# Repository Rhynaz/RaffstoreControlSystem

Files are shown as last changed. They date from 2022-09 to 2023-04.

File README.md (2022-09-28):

# Raffstore Control System (RCS)
> Web enabled relay board with hardware button support for easy smart home integration

## Features
Hardware:
- 9 - 30 VDC power supply
- ESP32-S3 Microcontroller
- 7 channels with two inputs and two outputs each
- inputs and outputs rated for 230 VAC / 325DC
- inputs and outputs galvanically isolated
- outputs fused
- outputs mutually exclusive (both off, only one on)
- 10-100 Mbps Ethernet connection
- 2.4 GHz 802.11 b/g/n Wi-Fi connection
- UART connection
- UART and JTAG over USB-B

Software:
- simple HTTP API with per and all channel controls
- Wi-Fi fallback if no Ethernet connection
- web interface based on simple HTTP API (See [Web Interface and HTTP API](#web-interface-and-http-api))
- time based automatic output disabling (See [Stop Timeout](#stop-timeout))
- [hardware button pattern recognition](#hardware-buttons)
- simple profile based [configuration](#project-configuration)
- [OTA update support](#firmware-upgrade)

## Repository Layout
| Path | Description |
| :---: | :---: |
| `hardware/` | KiCad 6 schematics and pcb layout |
| `software/` | ESP-IDF component directory |
| `software/config/` | [firmware config system](#project-configuration) |
| `software/controller/` | relay and switch controller handling hardware I/O |
| `software/http/` | web server serving the web interface and HTTP API |
| `software/main/` | firmware entrypoint |
|  `software/network/` | background network service |
| `software/update/` | [OTA update](#firmware-upgrade) service |
| `partitions.csv` | partition table for ESP32-S3 with 8 MB flash |
|  `sdkconfig.defaults`  | ESP-IDF project config for generating the full config |
| `thunder.json` | Thunder Client config for [OTA update](#firmware-upgrade) |

## Usage

### Web Interface and HTTP API
The web interface and HTTP API is served on port 80. Every channel can be opened (1st output on), closed (2nd output on) and stopped (both outputs off).
This can be done though the API by sending a `POST` request to `/actions/<action>/<channel_num>` where `<action>` is either `open`, `close` or `stop`, and `channel_num` is between including 0 and excluding the configured number of channels. Additionally channels can be controlled all at once by omiting the `/<channel_num>`. This is also possible in the web interface.

### Stop Timeout
Each channel has a configurable stop timeout, which is the longest time a channel has one of its output on. The timeout starts / resets with each open or close request.
After reaching the timeout the channel is stopped. This ensures minimal idle power usage and stress on the motor.

### Hardware Buttons
Two buttons are supported per channel and are used one for opening and the other for closing.
Each button supports basic pattern matching to accommodate three different control modes:
1. Press and hold to move the channel until the button is released.
2. Single click the button move the channel until the button is pressed again or the stop timeout is reached.
3. Double click the button to move all channel at the same time until the button is pressed again or the stop timeout is reached.

### Project Configuration
The configuration system utilizes `#define` statements from the currently active profile. A profile consists of a single header file in `software/config/include/config/profiles/` and an entry in `config/Kconfig`. It is recommended to create a copy of the default profile and start tweaking from there. The active config profile can be selected with ESP-IDF menuconfig under `Component Config > Raffstore Control System`.

### Firmware Upgrade
The firmware can be upgraded either over UART, USB or over-the-air (OTA) with HTTP over Ethernet or Wi-Fi. For the wired approaches use the ESP-IDF flashing tool and flash `build/RaffstoreControlSystem.elf`. The OTA update requires the use of a HTTP client (e.g. Thunder Client). To start the update, send a POST request to `/flash` with the firmware image as the body. Do not use multipart form data file upload, instead just put the raw binary data in the body. Use `build/RaffstoreControlSystem.bin` for OTA updates. The server will not send a response, it will apply the update and reboot. If the image gets corrupted during upload or flashing, the update is invalidated and the previous firmware will be used.

## License
RaffstoreControlSystem - Web enabled relay board with hardware button support for easy smart home integration<br>
Copyright (C) 2022 The Rhynaz

This program is free software: you can redistribute it and/or modify
it under the terms of the GNU General Public License as published by
the Free Software Foundation, either version 3 of the License, or
any later version.

This program is distributed in the hope that it will be useful,
but WITHOUT ANY WARRANTY; without even the implied warranty of
MERCHANTABILITY or FITNESS FOR A PARTICULAR PURPOSE. See the
GNU General Public License for more details.

You should have received a copy of the GNU General Public License
along with this program. If not, see <https://www.gnu.org/licenses/>.

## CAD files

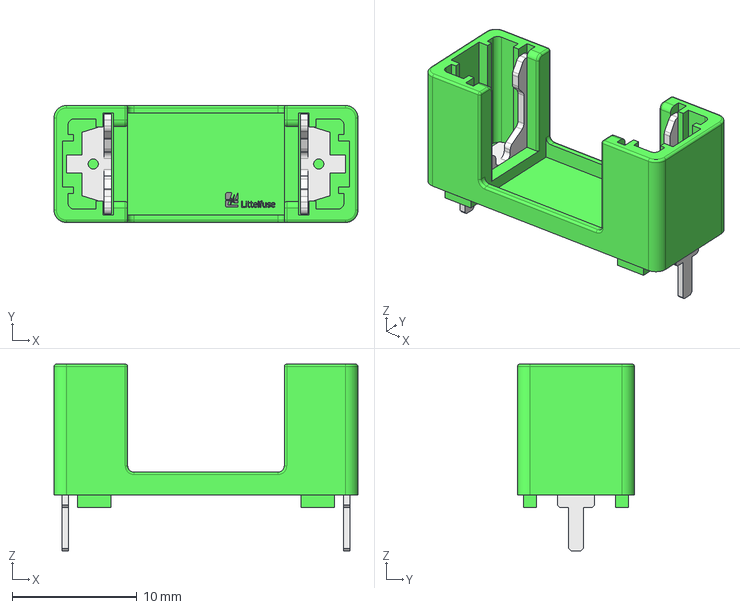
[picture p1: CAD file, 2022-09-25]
hardware/0PTF0078P/0PTF0078P.step
24.4 x 9.40 x 15.0 mm

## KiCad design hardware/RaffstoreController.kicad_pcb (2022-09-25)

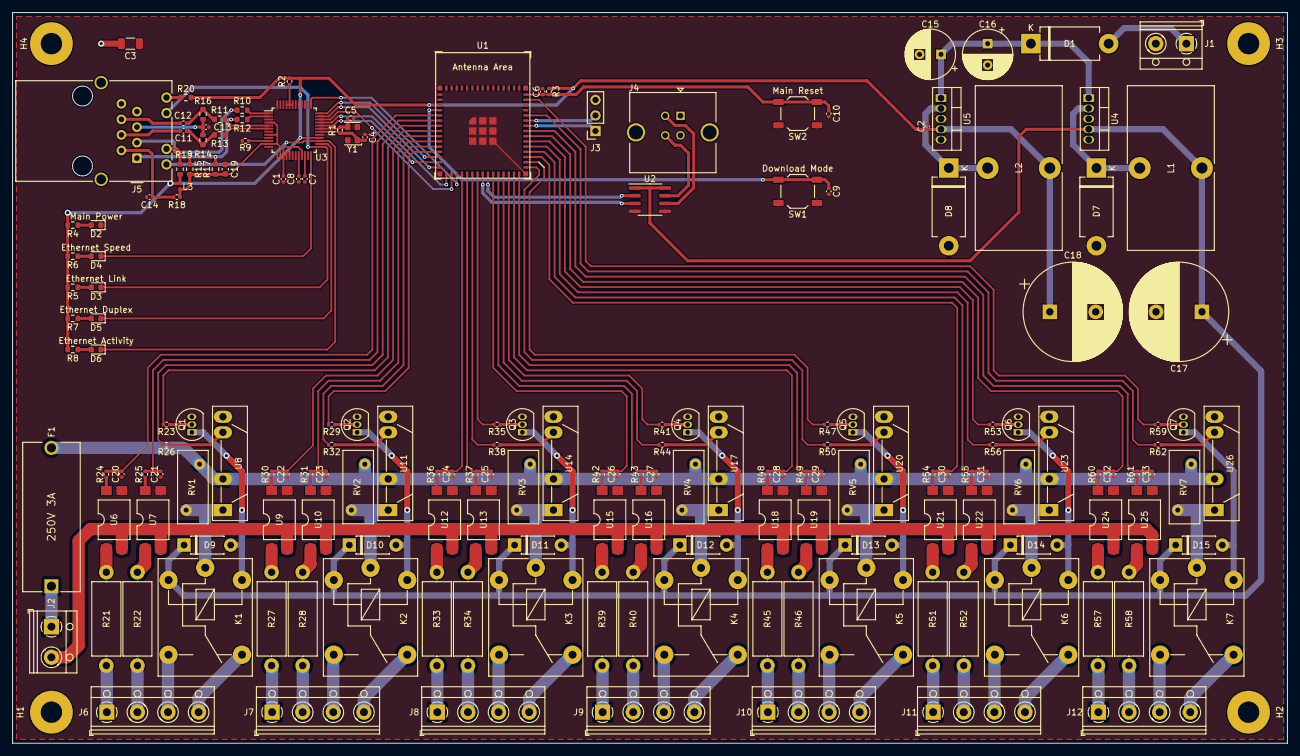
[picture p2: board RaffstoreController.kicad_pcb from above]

Board: 2 copper layers, 208.3 x 119.4 mm, 180 parts (0 on the bottom side), 167 nets.

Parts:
C1, C2, C9, C10: 100nF; C_0402_1005Metric
C3: 1nF; C_1206_3216Metric
C4, C5: 18pF; C_0402_1005Metric
C6, C20, C21, C22, C23, C24, C25, C26, C27, C28, C29, C30, C31, C32, C33: 1µF; C_0402_1005Metric
C7, C13: 10nF; C_0402_1005Metric
C8: 4.7µF; C_0402_1005Metric
C11, C12: 6.8nF; C_0402_1005Metric
C14: 22nF; C_0402_1005Metric
C15, C16: 100µF; CP_Radial_D8.0mm_P3.50mm
C17, C18: 1000µF; CP_Radial_D16.0mm_P7.50mm
C19: 10µF; C_0603_1608Metric
D1, D7, D8: 1N5822; D_DO-201AD_P12.70mm_Horizontal
D2: Main Power; LED_0603_1608Metric
D3: Ethernet Link; LED_0603_1608Metric
D4: Ethernet Speed; LED_0603_1608Metric
D5: Ethernet Duplex; LED_0603_1608Metric
D6: Ethernet Activity; LED_0603_1608Metric
D9, D10, D11, D12, D13, D14, D15: 1N4001; D_DO-41_SOD81_P7.62mm_Horizontal
F1: 250V 3A; 0PTF0078P
H1, H2, H3, H4: Mounting Hole; MountingHole_3.5mm_Pad
J1: DC 7-30V; TerminalBlock_RND_205-00012_1x02_P5.00mm_Horizontal
J2: AC 230V; TerminalBlock_RND_205-00012_1x02_P5.00mm_Horizontal
J3: Serial; PinSocket_1x03_P2.54mm_Vertical
J4: USB; USB_B_TE_5787834_Vertical
J5: 7499010121A; RJ45_Wuerth_7499010121A_Horizontal
J6, J7, J8, J9, J10, J11, J12: Raffstore; TerminalBlock_RND_205-00014_1x04_P5.00mm_Horizontal
K1, K2, K3, K4, K5, K6, K7: FINDER-36.11.9.005; Relay_SPDT_Finder_36.11
L1, L2: 100µH; L_Toroid_Vertical_L26.7mm_W14.0mm_P10.16mm_Pulse_D
L3: Ferrite Bead; L_0402_1005Metric
Q1, Q2, Q3, Q4, Q5, Q6, Q7: BC337; TO-92_Inline
R1: 1MΩ; R_0402_1005Metric
R2, R3, R23, R29, R35, R41, R47, R53, R59: 10kΩ; R_0402_1005Metric
R4, R5, R8, R19, R20: 62Ω; R_0603_1608Metric
R6, R7: 20Ω; R_0603_1608Metric
R9: 12.4kΩ; R_0402_1005Metric
R10, R11, R12, R13: 33Ω; R_0603_1608Metric
R14, R16: 82Ω; R_0603_1608Metric
R15, R17: 49.9Ω; R_0603_1608Metric
R18: 10Ω; R_0402_1005Metric
R21, R22, R27, R28, R33, R34, R39, R40, R45, R46, R51, R52, R57, R58: 430kΩ; R_Axial_DIN0414_L11.9mm_D4.5mm_P15.24mm_Horizontal
R24, R25, R30, R31, R36, R37, R42, R43, R48, R49, R54, R55, R60, R61: 1kΩ; R_0402_1005Metric
R26, R32, R38, R44, R50, R56, R62: 100Ω; R_0402_1005Metric
RV1, RV2, RV3, RV4, RV5, RV6, RV7: S10K275; RV_Disc_D12mm_W5mm_P7.5mm
SW1: Download Mode; SW_SPST_TL3342
SW2: Main Reset; SW_SPST_TL3342
U1: ESP32-S3-MINI-1
U2: USB6B1; SOIC-8_3.9x4.9mm_P1.27mm
U3: W5500; LQFP-48_7x7mm_P0.5mm
U4: LM2576T-5; TO-220-5_Vertical
U5: LM2576T-3.3; TO-220-5_Vertical
U6, U7, U9, U10, U12, U13, U15, U16, U18, U19, U21, U22, U24, U25: SFH6286-3T; SMDIP-4_W9.53mm_Clearance8mm
U8, U11, U14, U17, U20, U23, U26: S202S02; SIP4_Sharp-SSR_P7.62mm_Straight
Y1: 25MHz; Oscillator_SMD_EuroQuartz_XO32-4Pin_3.2x2.5mm

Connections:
+3.3VA: C1.2, C19.1, L3.2, R15.1, R17.1, R18.1, U3.4 (AVDD), U3.8 (AVDD), U3.11 (AVDD), U3.15 (AVDD), U3.17 (AVDD), U3.21 (AVDD)
+3V3: C2.2, C18.1, L2.2, L3.1, R2.1, R3.1, R4.2, R5.2, R6.2, R7.2, R8.2, R19.1, R20.2, U1.3 (3V3), U3.28 (VDD), U5.4 (FB)
+5V: C17.1, D9.1 (K), D10.1 (K), D11.1 (K), D12.1 (K), D13.1 (K), D14.1 (K), D15.1 (K), K1.A1, K2.A1, K3.A1, K4.A1, K5.A1, K6.A1, K7.A1, L1.2, U2.1 (VBUS), U2.8 (VBUS), U4.4 (FB)
/CLK: U1.16 (IO12/SPI_CLK), U3.33 (SCLK)
/D+: U1.24 (IO20/USB_D+), U2.2 (I/O1)
/D-: U1.23 (IO19/USB_D-), U2.3 (I/O2)
/IO1: C20.1, R24.2, U1.5 (IO01)
/IO2: C21.1, R25.2, U1.6 (IO02)
/IO3: R26.2, U1.7 (IO03)
/IO4: R23.2, U1.8 (IO04)
/IO5: C22.1, R30.2, U1.9 (IO05)
/IO6: C23.1, R31.2, U1.10 (IO06)
/IO7: R32.2, U1.11 (IO07)
/IO8: R29.2, U1.12 (IO08)
/IO15: C24.1, R36.2, U1.19 (IO15)
/IO16: C25.1, R37.2, U1.20 (IO16)
/IO17: R38.2, U1.21 (IO17)
/IO18: R35.2, U1.22 (IO18)
/IO21: C26.1, R42.2, U1.25 (IO21)
/IO26: C27.1, R43.2, U1.26 (IO26)
/IO33: R41.2, U1.28 (IO33)
/IO34: C28.1, R48.2, U1.29 (IO34)
/IO35: R50.2, U1.31 (IO35)
/IO36: R47.2, U1.32 (IO36)
/IO37: C30.1, R54.2, U1.33 (IO37)
/IO38: C31.1, R55.2, U1.34 (IO38)
/IO39: R56.2, U1.35 (IO39)
/IO40: R53.2, U1.36 (IO40)
/IO41: C32.1, R60.2, U1.37 (IO41)
/IO42: C33.1, R61.2, U1.38 (IO42)
/IO45: R62.2, U1.41 (IO45)
/IO46: R59.2, U1.44 (IO46)
/IO47: R44.2, U1.27 (IO47)
/IO48: C29.1, R49.2, U1.30 (IO48)
/MISO: U1.17 (IO13/SPI_MISO), U3.34 (MISO)
/MOSI: U1.15 (IO11/SPI_MOSI), U3.35 (MOSI)
/RD+: C11.2, J5.4 (RD+)
/RD-: C12.2, J5.6 (RD-)
/RX: J3.2, U1.40 (UART_RX/IO44)
/RX+: R13.1, U3.6 (RXP)
/RX-: R11.1, U3.5 (RXN)
/Raffstore Channel 0/MotorClose: J6.4, K1.12
/Raffstore Channel 0/MotorOpen: J6.3, K1.14
/Raffstore Channel 0/SwitchClose: J6.2, R22.1
/Raffstore Channel 0/SwitchOpen: J6.1, R21.1
/Raffstore Channel 1/MotorClose: J7.4, K2.12
/Raffstore Channel 1/MotorOpen: J7.3, K2.14
/Raffstore Channel 1/SwitchClose: J7.2, R28.1
/Raffstore Channel 1/SwitchOpen: J7.1, R27.1
/Raffstore Channel 2/MotorClose: J8.4, K3.12
/Raffstore Channel 2/MotorOpen: J8.3, K3.14
/Raffstore Channel 2/SwitchClose: J8.2, R34.1
/Raffstore Channel 2/SwitchOpen: J8.1, R33.1
/Raffstore Channel 3/MotorClose: J9.4, K4.12
/Raffstore Channel 3/MotorOpen: J9.3, K4.14
/Raffstore Channel 3/SwitchClose: J9.2, R40.1
/Raffstore Channel 3/SwitchOpen: J9.1, R39.1
/Raffstore Channel 4/MotorClose: J10.4, K5.12
/Raffstore Channel 4/MotorOpen: J10.3, K5.14
/Raffstore Channel 4/SwitchClose: J10.2, R46.1
/Raffstore Channel 4/SwitchOpen: J10.1, R45.1
/Raffstore Channel 5/MotorClose: J11.4, K6.12
/Raffstore Channel 5/MotorOpen: J11.3, K6.14
/Raffstore Channel 5/SwitchClose: J11.2, R52.1
/Raffstore Channel 5/SwitchOpen: J11.1, R51.1
/Raffstore Channel 6/MotorClose: J12.4, K7.12
/Raffstore Channel 6/MotorOpen: J12.3, K7.14
/Raffstore Channel 6/SwitchClose: J12.2, R58.1
/Raffstore Channel 6/SwitchOpen: J12.1, R57.1
/TD+: J5.1 (TD+), R12.2, R17.2
/TD-: J5.3 (TD-), R10.2, R15.2
/TX: J3.1, U1.39 (UART_TX/IO43)
/TX+: R12.1, U3.2 (TXP)
/TX-: R10.1, U3.1 (TXN)
/~CS: U1.14 (IO10/~SPI_CS), U3.32 (~SCS)
/~INT: U1.13 (IO09/~SPI_INT), U3.36 (~INT)
/~RST: U1.18 (IO14/~SPI_RST), U3.37 (~RST)
AC: F1.2, RV1.2, RV2.2, RV3.2, RV4.2, RV5.2, RV6.2, RV7.2, U8.2, U11.2, U14.2, U17.2, U20.2, U23.2, U26.2
ACT_LED: D6.1 (K), J5.9, U3.27 (ACTLED)
CPU_DLM: C9.2, SW1.2, U1.4 (IO00/DLM)
CPU_RST: C6.1, C10.2, R3.2, SW2.2, U1.45 (EN)
DUP_LED: D5.1 (K), U3.26 (DUPLED)
GND: C1.1, C2.1, C3.1, C4.2, C5.2, C6.2, C7.2, C8.2, C9.1, C10.1, C13.2, C14.2, C15.2, C16.2, C17.2, C18.2, C19.2, C20.2, C21.2, C22.2, C23.2, C24.2, C25.2, C26.2, C27.2, C28.2, C29.2, C30.2, C31.2, C32.2, C33.2, D2.1 (K), D7.2 (A), D8.2 (A), J1.2, J3.3, J4.4 (GND), Q1.3 (E), Q2.3 (E), Q3.3 (E), Q4.3 (E), Q5.3 (E), Q6.3 (E), Q7.3 (E), R9.1, SW1.1, SW2.1, U1.1 (GND), U1.2 (GND), U1.42 (GND), U1.43 (GND), U1.46 (GND), U2.4 (GND), U2.5 (GND), U3.3 (AGND), U3.9 (AGND), U3.14 (AGND), U3.16 (AGND), U3.19 (AGND), U3.29 (GND), U3.48 (AGND), U4.3 (GND), U4.5 (~ON/OFF), U5.3 (GND), U5.5 (~ON/OFF), U6.3, U7.3, U8.4, U9.3, U10.3, U11.4, U12.3, U13.3, U14.4, U15.3, U16.3, U17.4, U18.3, U19.3, U20.4, U21.3, U22.3, U23.4, U24.3, U25.3, U26.4, Y1.2, Y1.4
GNDPWR: J2.2, U6.2, U7.2, U9.2, U10.2, U12.2, U13.2, U15.2, U16.2, U18.2, U19.2, U21.2, U22.2, U24.2, U25.2
GNDREF: C3.2, H1.1, H2.1, H3.1, H4.1, J4.5 (Shield), J5.8, J5.SH
LNK_LED: D3.1 (K), J5.11, U3.25 (LINKLED)
unnamed: C4.1, R1.2, U3.30 (XI/CLKIN), Y1.1
unnamed: C5.1, R1.1, U3.31 (XO), Y1.3
unnamed: C7.1, U3.22 (1V2O)
unnamed: C8.1, U3.20 (TOCAP)
unnamed: C11.1, R13.2, R14.2
unnamed: C12.1, R11.2, R16.2
unnamed: C13.1, J5.5 (RCT), R14.1, R16.1
unnamed: C14.1, J5.2 (TCT), R18.2
unnamed: D1.2 (A), J1.1
unnamed: D2.2 (A), R4.1
unnamed: D3.2 (A), R5.1
unnamed: D4.2 (A), R6.1
unnamed: D5.2 (A), R7.1
unnamed: D6.2 (A), R8.1
unnamed: D7.1 (K), L1.1, U4.2 (OUT)
unnamed: D8.1 (K), L2.1, U5.2 (OUT)
unnamed: D9.2 (A), K1.A2, Q1.1 (C)
unnamed: D10.2 (A), K2.A2, Q2.1 (C)
unnamed: D11.2 (A), K3.A2, Q3.1 (C)
unnamed: D12.2 (A), K4.A2, Q4.1 (C)
unnamed: D13.2 (A), K5.A2, Q5.1 (C)
unnamed: D14.2 (A), K6.A2, Q6.1 (C)
unnamed: D15.2 (A), K7.A2, Q7.1 (C)
unnamed: F1.1, J2.1
unnamed: J4.2 (D-), U2.6 (I/O2)
unnamed: J4.3 (D+), U2.7 (I/O1)
unnamed: J5.10, R19.2
unnamed: J5.12, R20.1
unnamed: K1.11, RV1.1, U8.1
unnamed: K2.11, RV2.1, U11.1
unnamed: K3.11, RV3.1, U14.1
unnamed: K4.11, RV4.1, U17.1
unnamed: K5.11, RV5.1, U20.1
unnamed: K6.11, RV6.1, U23.1
unnamed: K7.11, RV7.1, U26.1
unnamed: Q1.2 (B), R23.1
unnamed: Q2.2 (B), R29.1
unnamed: Q3.2 (B), R35.1
unnamed: Q4.2 (B), R41.1
unnamed: Q5.2 (B), R47.1
unnamed: Q6.2 (B), R53.1
unnamed: Q7.2 (B), R59.1
unnamed: R2.2, U3.43 (PMODE2), U3.44 (PMODE1), U3.45 (PMODE0)
unnamed: R9.2, U3.10 (EXRES1)
unnamed: R21.2, U6.1
unnamed: R22.2, U7.1
unnamed: R24.1, U6.4
unnamed: R25.1, U7.4
unnamed: R26.1, U8.3
unnamed: R27.2, U9.1
unnamed: R28.2, U10.1
unnamed: R30.1, U9.4
unnamed: R31.1, U10.4
unnamed: R32.1, U11.3
unnamed: R33.2, U12.1
unnamed: R34.2, U13.1
unnamed: R36.1, U12.4
unnamed: R37.1, U13.4
unnamed: R38.1, U14.3
unnamed: R39.2, U15.1
unnamed: R40.2, U16.1
unnamed: R42.1, U15.4
unnamed: R43.1, U16.4
unnamed: R44.1, U17.3
unnamed: R45.2, U18.1
unnamed: R46.2, U19.1
unnamed: R48.1, U18.4
unnamed: R49.1, U19.4
unnamed: R50.1, U20.3
unnamed: R51.2, U21.1
unnamed: R52.2, U22.1
unnamed: R54.1, U21.4
unnamed: R55.1, U22.4
unnamed: R56.1, U23.3
unnamed: R57.2, U24.1
unnamed: R58.2, U25.1
unnamed: R60.1, U24.4
unnamed: R61.1, U25.4
unnamed: R62.1, U26.3
SPD_LED: D4.1 (K), U3.24 (SPDLED)
VCC: C15.1, C16.1, D1.1 (K), U4.1 (VIN), U5.1 (VIN)

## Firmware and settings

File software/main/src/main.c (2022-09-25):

#include "network.h"
#include "controller.h"
#include "http.h"
#include "update.h"

#include "esp_log.h"
#include "esp_event.h"
#include "driver/gpio.h"

static const char *const TAG = "Main       ";

void app_main()
{
    ESP_LOGI(TAG, "Raffstore Control System");
    ESP_LOGI(TAG, "Version " CONFIG_APP_PROJECT_VER);

    ESP_LOGI(TAG, "Register global ISR handler.");
    ESP_ERROR_CHECK(gpio_install_isr_service(0));

    ESP_LOGI(TAG, "Create default event loop.");
    ESP_ERROR_CHECK(esp_event_loop_create_default());

    ESP_LOGI(TAG, "Initialize network stack.");
    network_init();

    ESP_LOGI(TAG, "Initialize controller.");
    controller_init();

    ESP_LOGI(TAG, "Initialize HTTP server.");
    http_init();

    update_mark_valid();
}

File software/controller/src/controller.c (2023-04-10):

#include "controller.h"

#include "controller/channel.h"

#include "config.h"

#include "esp_log.h"
#include "esp_event.h"
#include "driver/gpio.h"

#define CONTROLLER_DEFINE_CHANNEL(num)                                         \
    [CONFIG_CONTROLLER_CHANNEL##num##_INDEX] = (channel_t)                     \
    {                                                                          \
        .index = CONFIG_CONTROLLER_CHANNEL##num##_INDEX,                       \
        .stop_timeout_sec = CONFIG_CONTROLLER_CHANNEL##num##_STOP_TIMEOUT_SEC, \
        .motor_enable = CONFIG_CONTROLLER_CHANNEL##num##_MOTOR_ENABLE,         \
        .motor_direction = CONFIG_CONTROLLER_CHANNEL##num##_MOTOR_DIRECTION,   \
        .motor_invert = CONFIG_CONTROLLER_CHANNEL##num##_MOTOR_INVERT,         \
        .switch_up = CONFIG_CONTROLLER_CHANNEL##num##_SWITCH_UP,               \
        .switch_down = CONFIG_CONTROLLER_CHANNEL##num##_SWITCH_DOWN,           \
        .switch_invert = CONFIG_CONTROLLER_CHANNEL##num##_SWITCH_INVERT,       \
    }

static const char *const TAG = "Controller ";

static channel_t channels[CONFIG_CONTROLLER_CHANNEL_NUM] = {
#ifdef CONFIG_CONTROLLER_CHANNEL0_ENABLE
    CONTROLLER_DEFINE_CHANNEL(0),
#endif
#ifdef CONFIG_CONTROLLER_CHANNEL1_ENABLE
    CONTROLLER_DEFINE_CHANNEL(1),
#endif
#ifdef CONFIG_CONTROLLER_CHANNEL2_ENABLE
    CONTROLLER_DEFINE_CHANNEL(2),
#endif
#ifdef CONFIG_CONTROLLER_CHANNEL3_ENABLE
    CONTROLLER_DEFINE_CHANNEL(3),
#endif
#ifdef CONFIG_CONTROLLER_CHANNEL4_ENABLE
    CONTROLLER_DEFINE_CHANNEL(4),
#endif
#ifdef CONFIG_CONTROLLER_CHANNEL5_ENABLE
    CONTROLLER_DEFINE_CHANNEL(5),
#endif
#ifdef CONFIG_CONTROLLER_CHANNEL6_ENABLE
    CONTROLLER_DEFINE_CHANNEL(6),
#endif
};

void controller_init()
{
    ESP_LOGI(TAG, "Configure GPIOs.");
    gpio_config_t switch_config = {
        .pin_bit_mask = 0,
        .mode = GPIO_MODE_INPUT,
        .pull_up_en = GPIO_PULLUP_ENABLE,
        .pull_down_en = GPIO_PULLDOWN_DISABLE,
        .intr_type = GPIO_INTR_DISABLE,
    };

    gpio_config_t motor_config = {
        .pin_bit_mask = 0,
        .mode = GPIO_MODE_INPUT_OUTPUT,
        .pull_up_en = GPIO_PULLUP_DISABLE,
        .pull_down_en = GPIO_PULLDOWN_DISABLE,
        .intr_type = GPIO_INTR_DISABLE,
    };

    for (uint8_t i = 0; i < CONFIG_CONTROLLER_CHANNEL_NUM; i++)
    {
        switch_config.pin_bit_mask |= (1ULL << channels[i].switch_up) | (1ULL << channels[i].switch_down);
        motor_config.pin_bit_mask |= (1ULL << channels[i].motor_enable) | (1ULL << channels[i].motor_direction);
    }

    ESP_ERROR_CHECK(gpio_config(&switch_config));
    ESP_ERROR_CHECK(gpio_config(&motor_config));

    ESP_LOGI(TAG, "Initialize channels.");
    for (uint8_t i = 0; i < CONFIG_CONTROLLER_CHANNEL_NUM; i++)
        channel_init(&channels[i]);
}

void controller_open(uint8_t channel_num, bool user_initiated)
{
    if (channel_num >= CONFIG_CONTROLLER_CHANNEL_NUM)
    {
        ESP_LOGE(TAG, "Tried opening channel %u of %u.", channel_num, CONFIG_CONTROLLER_CHANNEL_NUM);
        return;
    }

    esp_event_post_to(channels[channel_num].event_loop, CHANNEL_EVENT, CHANNEL_EVENT_OPEN, &user_initiated, sizeof(user_initiated), 0);
}

void controller_open_all(bool user_initiated)
{
    ESP_LOGI(TAG, "Open all channels.");

    for (uint8_t i = 0; i < CONFIG_CONTROLLER_CHANNEL_NUM; i++)
    {
        controller_open(i, user_initiated);
    }
}

void controller_close(uint8_t channel_num, bool user_initiated)
{
    if (channel_num >= CONFIG_CONTROLLER_CHANNEL_NUM)
    {
        ESP_LOGE(TAG, "Tried closing channel %u of %u.", channel_num, CONFIG_CONTROLLER_CHANNEL_NUM);
        return;
    }

    esp_event_post_to(channels[channel_num].event_loop, CHANNEL_EVENT, CHANNEL_EVENT_CLOSE, &user_initiated, sizeof(user_initiated), 0);
}

void controller_close_all(bool user_initiated)
{
    ESP_LOGI(TAG, "Close all channels.");

    for (uint8_t i = 0; i < CONFIG_CONTROLLER_CHANNEL_NUM; i++)
    {
        controller_close(i, user_initiated);
    }
}

void controller_stop(uint8_t channel_num, bool user_initiated)
{
    if (channel_num >= CONFIG_CONTROLLER_CHANNEL_NUM)
    {
        ESP_LOGE(TAG, "Tried stopping channel %u of %u.", channel_num, CONFIG_CONTROLLER_CHANNEL_NUM);
        return;
    }

    esp_event_post_to(channels[channel_num].event_loop, CHANNEL_EVENT, CHANNEL_EVENT_STOP, &user_initiated, sizeof(user_initiated), 0);
}

void controller_stop_all(bool user_initiated)
{
    ESP_LOGI(TAG, "Stop all channels.");

    for (uint8_t i = 0; i < CONFIG_CONTROLLER_CHANNEL_NUM; i++)
    {
        controller_stop(i, user_initiated);
    }
}

int8_t controller_query(uint8_t channel_num)
{
    if (channel_num >= CONFIG_CONTROLLER_CHANNEL_NUM)
    {
        ESP_LOGE(TAG, "Tried querying channel %u of %u.", channel_num, CONFIG_CONTROLLER_CHANNEL_NUM);
        return -1;
    }

    return channels[channel_num].last_user_event;
}

int8_t *controller_query_all()
{
    ESP_LOGI(TAG, "Query all channels.");

    static int8_t results[CONFIG_CONTROLLER_CHANNEL_NUM + 1];
    results[CONFIG_CONTROLLER_CHANNEL_NUM] = -1;

    for (uint8_t i = 0; i < CONFIG_CONTROLLER_CHANNEL_NUM; i++)
    {
        results[i] = controller_query(i);
    }

    return results;
}

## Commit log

2022-09-25 Open Source RCS v1.0.0
    [0PTF0078P.step, RaffstoreChannel.kicad_sch, RaffstoreController.kicad_pcb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]
2022-09-27 Update version to 1.1.0
    Add LICENSE
    Add double click on hardware buttons
    Fix missing check in motor_stop_if_moving
    [channel.c, default.h, rcseg.h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]
